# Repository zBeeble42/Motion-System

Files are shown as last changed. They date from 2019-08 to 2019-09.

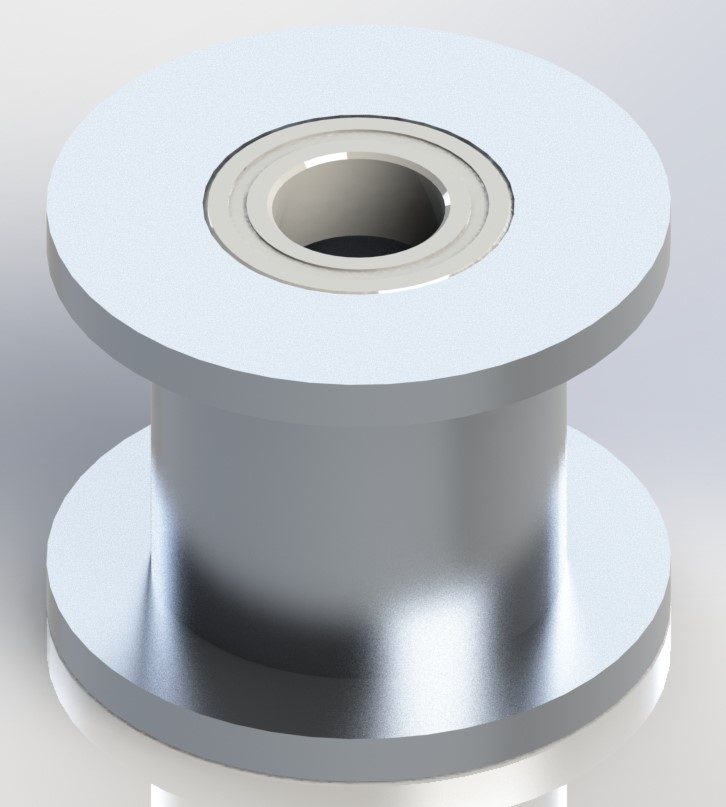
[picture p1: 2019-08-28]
Solidworks/1037396.JPG

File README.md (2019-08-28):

# Motion System
STPs / STLs / DXFs / PDFs

E3D-Online Ltd: Copyright (C) E3D-Online Ltd (e3d-online.com) These files are free hardware you can redistribute it and / or modify it under the terms of the General Public License as published by the Free Software Foundation, either version 3 of the License, or (at your option) any later version.
McMaster Carr: Copyright (C) McMaster Carr (mcmastercarr.com) The CAD models are being made available to help you decide whether to purchase products from us.  No other use is authorized or granted.
  
---------------------------------------------------------------------------------------------------------------------------------------
TODO:
 - Add in the purchasable hardware.
 - Modify the toolhead printed boden tube\wire harness mount to be one printed item and strain relief the boden tube and wire harness better.
 - Finish the Bondtech BMG-M toolhead assembly.
 - Create 
---------------------------------------------------------------------------------------------------------------------------------------
TIMELINE:
 08/28/19 - (Me) Added progress to the motion system assembly, and updadted the BOM with purchasable items (some to replace machineable parts from the E3d Github master repo).  I also added an "attempt" to create a tool head for the Bondtech BMG-M direct drive extruder. 

 08/15/19 - (Me) Added BOM

 08/13/19 - (Me) Forked from E3D Online, and started adding Solidworks 2017 files

 05/08/19 - (E3D) Added README.md to the STLs folder  

 02/08/19 - (E3D) Added assembly drawings

 31/07/19 - (E3D) Added step files of printed parts

 30/07/19 - (E3D) Initial Upload

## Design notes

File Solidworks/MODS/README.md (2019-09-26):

This modified version of E3D's toolchanger uses a more commonly found 24BYJ48 micro stepper motor with the two "ears".

The machined aluminium 'TC-BACK_1_1.sldprt' -> 'TC_BACK_1_2.sldprt' and 
the 3D printed 'Tool-Changer Cover Body.sldprt' -> 'Tool-Changer Cover Body_1.1.sldprt' 
parts have been modified to fit these motors.

I have not tested any motors with this new design, so use this at your own risk.

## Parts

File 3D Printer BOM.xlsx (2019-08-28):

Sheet: Hardware
Item # | Description | Supplier | Part Number | Qty | Units | Cost/Pc | Pur Cost | Order Qty | CAD?
1 | Knife |  |  | 1 | ea
2 | 5mm Allen Key |  |  | 1 | ea
3 | 4mm Allen Key |  |  | 1 | ea
4 | 2.5mm Allen Key |  |  | 1 | ea
5 | 2mm Allen Key |  |  | 1 | ea
6 | Bubble Level |  |  | 1 | ea
7 | Machinist Square |  |  | 1 | ea
8 | Gel Thread Lock (Blue) | McM | 1810A3 | 1.69 | floz |  | $28.93 | 1.69
9 | Isocyanate Glue |  |  | 1 | floz
10 | Small Side Cutters |  |  | 1 | ea
47 | Thickened PTFE Grease |  |  | 0.75 | floz
11 | M3 Thread Tap | McM | 2541A31 | 1 | ea |  | $15.80 | 1
12 | M8 Thread Tap | McM | 2541A35 | 1 | ea |  | $19.20 | 1
13 | 25-2560 x 500mm Al Extrusion |  |  | 4 | ea
 | M2 x 6mm SHCS
14 | M2 Washers | McM | 93475A195 | 8 | ea |  | $1.06 | 100 | Yes
15 | M2.5 x 5mm SHCS | McM | 91292A009 | 1 | ea |  | $4.97 | 100 | Yes
16 | M3 x 3mm FHCS |  |  | 4 | ea
17 | M3 x 5mm BHCS | McM | 92095A177 | 7 | ea |  | $6.12 | 100 | Yes
18 | M3 x 8mm SHCS | McM | 91292A112 | 4 | ea |  | $4.52 | 100 | Yes
19 | M3 x 8mm FHCS | McM | 92125A128 | 4 | ea |  | $3.54 | 100 | Yes
20 | M3 x 10mm SHCS | McM | 91292A113 | 1 | ea |  | $4.97 | 100 | Yes
21 | M3 x 10mm BHCS | McM
22 | M3 x 12mm FHCS | McM | 92125A132 | 24 | ea |  | $4.97 | 100 | Yes
23 | M3 x 12mm BHCS
24 | M3 x 16mm FHCS | McM | 92125A134 | 8 | ea |  | $8.28 | 100 | Yes
25 | M3 x 30mm BHCS
26 | M3 x 45mm BHCS
27 | M3 x 50mm FHCS | McM | 92125A151 | 2 | ea |  | $6.70 | 50 | Yes
28 | M3 x 10mm Low Profile Sholder Screw | McM | 90323A215 | 10 | ea |  | $2.75 | ea >5
31 | M3 x 3mm Grub Screw |  |  | 1 | ea
32 | M3 x 12mm PEEK Standoffs |  |  | 4 | ea
33 | M3 Standoffs | McM | 93655A419 | 10 | ea |  | $3.20 | ea >10 | Yes
 | M3 x 4mm unthreaded standoff (replaces MS-XY-STOP) | McM | 92871A173 | 4 | ea
34 | M3 x 24mm (6mm hex) (Replaces MS-SOFF-M3-FF-24L) | McM | 94868A743 | 2 | ea |  | $6.61 | ea | Yes
29 | M3 Washers | McM | 93475A210 | 62 | ea |  | $1.62 | 100 | Yes
30 | M3 Hex Half Nuts |  |  | 4 | ea
35 | M4 x 3mm Grub Screw |  |  | 1 | ea
36 | M4 x 8mm BHCS |  |  | 16 | ea
37 | M4 x 6mm BHCS |  |  | 17 | ea
38 | M4 x 12mm BHCS |  |  | 4 | ea
39 | M4 x 16mm BHCS |  |  | 2 | ea
40 | M4 x 10mm BHCS |  | 92095A190 | 4 | ea |  | $9.05 | 100 | Yes
41 | M4 x 10mm Low Profile Sholder Screw (Replaces MS-SHAFT-BOLT) | McM | 90318A810 | 10 | ea |  | $3.13 | ea >5 | Yes
 | M4 x 4mm - 6mm OD Standoffs (Replaces MS-Z-STOP) |  | 92871A006 | 2 | ea |  | $1.89 | ea | Yes
42 | M4 x 12mm Standoffs |  |  | 8 | ea
43 | M4 Washers |  | 93475A230 | 15 | ea |  | $1.86 | 100 | Yes
44 | M4 Nylon Washers |  |  | 8 | ea
45 | M4 Hex Half Nuts |  |  | 2 | ea
46 | M6 T-Nuts |  | 5537T527 | 28 | ea |  | $5.08 | 4
47 | M6 x 10mm BHCS |  |  | 25 | ea
48 | M6 Washers |  |  | 24 | ea
49 | M6 Grub Screw |  |  | 4 | ea
50 | M8 Feet | McM | 6301K79 | 5 | ea |  | $6.20 | 1
51 | M8 x 20mm BHCS |  | 92095A284 | 15 | ea |  | $13.64 | 25
52 | E-Clip |  | 98317A214 | 1 | ea |  | $9.86 | 50
53 | 3mm x 12mm Dowel |  | 91595A112 | 1 | ea |  | $8.62 | 50
54 | 1mm x 4mm Dowel |  | 91585A034 | 6 | ea |  | $8.63 | 100
55 | Thickened PTFE Grease |  |  | 0.75 | floz
56 | MR1052ZZ bearing |  | 7804K106 | 1 | ea |  | $7.60 | 1
57 | SF695ZZ Bearing (695-2Z) |  | 7804K138 | 1 | ea |  | $9.20 | 1
58 | F5-12M bearing |  | 7806K57 | 1 | ea |  | $8.66 | 1
59 | Spring |  |  | 1 | ea
60 | Zip Ties
61 | Fray-Resistant Expandable Sleeving, Fray-Resistant, 1/8" ID |  |  | 10 | ft
62 | Braided Sleeve
63 | Metal Strips |  |  | 5 | ea
64 | 2.54mm Crimp Terminal (22-28 Gauge) |  |  | 100 | pcs
65 | 790mm lengths of PTFE tubing |  |  | 4 | ea
66 | 850mm lengths of PTFE tubing |  |  | 4 | ea
67 | Lay-in Snap-Together Open Cable/Hose Carrier for 0.5" Maximum Cable OD/0.5" Total Cable Width, 0.9" High |  |  | 1 | ft
68 | 6.25mm x 7.0mm Neodymium Magnet |  |  | 4 | ea

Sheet: Electrical
Item # | Description | Part Number | Qty | Units
 | Duet2 WiFi/ Ethernet |  | 1 | ea
 | DueX5 |  | 1 | ea
 | Power Supply - S-400-24 |  | 1 | ea
 | SSR G3NA-210B-UTU |  | 1 | ea
 | 300mm x 200mm Heated Bed 24VDC |  | 1 | ea
 | Duet Wiring Kit |  | 1 | ea
 | Panel Mount RJ45 Connector |  | 1 | ea
 | Axis Motors (1.8deg @ 2A) | Moons MS17HD2P4200 | 2
 | Extruder motors | MOTECH MT-1703HSM1168RE .9 deg/step | 4
 | X-Axis Hiwin Rail | MGNR9H 180dq 10200 | 1
 | Y-Axis Hiwin Rail | MGNR12H 180DQ 5000 | 2
 | Z-Axis Hiwin Rail | MGWR12H 180DQ0 40100 | 1

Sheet: 3D Printed Parts
Item # | Description | Qty | Units
 | Printed V6 Dock Cables | 2
 | Printed V6 Dock Cables (Mirror) | 2
 | Printed Spool Carrier | 4
 | Printed Filament Pick-Up | 4
 | Printed PSU Duct | 1
 | Printed Cable Blank | 1
 | Printed RJ45 Cable Blank (Optional) | 1
 | Printed Wiper Brush Holder | 1
 | Printed IEC Socket | 1
 | Printed IEC Bracket | 1
 | Printed X-Carriage Cable Bracket | 2
 | Printed Tool-Changer Cover | 1
 | Printed Motor Cable Cover | 1
 | Printed Z-Axis Motor Cable Cover | 1
 | Printed MS-BELT-CLAMP | 4

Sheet: Machined Parts
Item # | Description | Qty | Units
1 | 8mm x 90mm Metal Bar (Spool Bar) | 4
5 | MS-LONG-PULLEY-STANDOFF | 4
6 | MS-MOTOR-SPACE-SHORT | 4
7 | MS-SOFF-M3-FF-24L_1 | 2
8 | MS-SHAFT-BOLT | 10
9 | MS-SHORT-PULLEY-STANDOFF | 10
10 | MS-TOP-PLATE | 1
11 | MS-BASE-PLATE | 1
12 | MS-SIDE-PANEL | 2
13 | MS-ELEC-PANEL | 1
14 | MS-REAR-PANEL | 1
15 | MS-BED-BRACKET | 1
16 | MS-TENSION-BLOCK | 2
17 | MS-TENSION-ARM | 2
18 | MS-Z-STOP | 2
19 | MS-XY-STOP | 4
20 | Z-Axis Bed Bearing Bracket | 1
21 | Z-Axis Angle Motor Bracket | 1
22 | X-Plate | 1
23 | Z-AXIS BED PLATE | 1
24 | MS-X-BELT-PLATE | 1
25 | MS-X-BLOCK | 1
26 | MS-X-SPACER | 2
27 | MS-BED-BRACKET | 1
28 | TC-MOD 0.5-20T-SERVO-GEAR | 1
29 | TC-MOTOR-BRACKET | 1
30 | TC-FACE | 1
31 | TC-HE-V6 | 1
32 | TC-V6-DOCK | 4
33 | TC-DOCK-V6 | 1
34 | TC-PLATE | 1
35 | TC-RAMP-6MM | 1
36 | TC-BACK | 1
37 | TC-DOCK-PIN-V6 | 8
38 | TC-SHAFT | 1

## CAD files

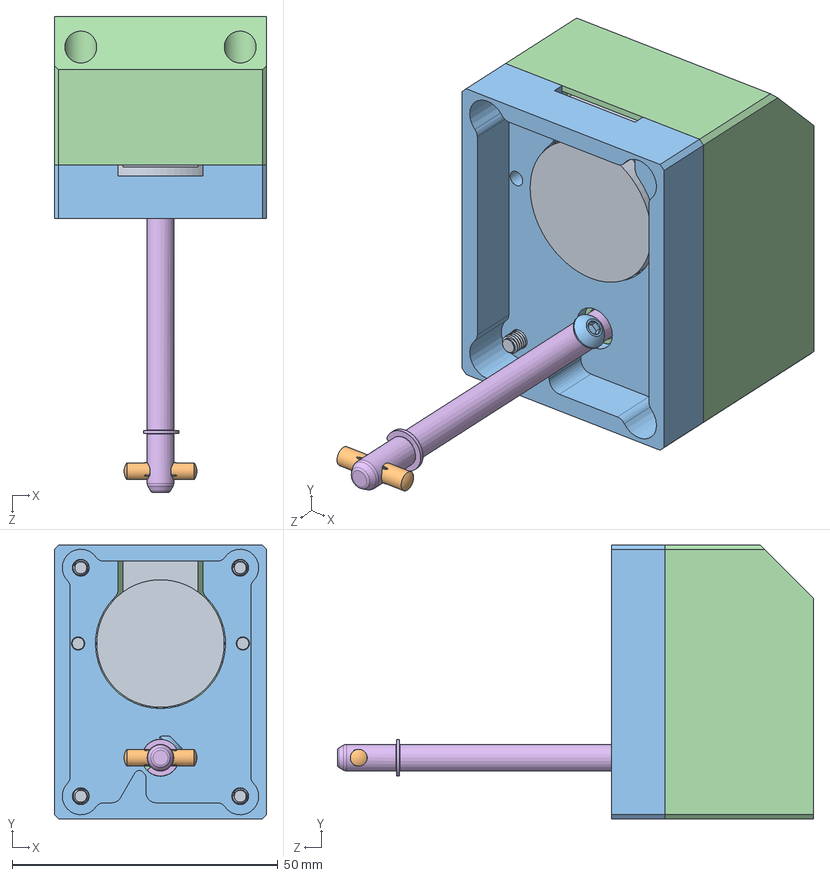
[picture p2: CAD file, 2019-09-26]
Solidworks/MODS/Tool Changer Front v2.sldasm
40.0 x 51.5 x 89.6 mm
93655A419_MALE-FEMALE THREADED HEX STANDOFF x 6
91292A110_TYPE 18-8 SS SOCKET HEAD CAP SCREW x 4
92095A471_18-8 SS BUTTON-HEAD SOCKET CAP SCREW x 4
7804K106_STAINLESS STEEL BALL BEARING MR105RS
7806K570_F5-12 Thrust bearing
98543A103_SIDE-MOUNT EXTERNAL RETAINING RING E-STYLE
94125K671_COMPRESSION SPRINGS
98269A420_BLACK-OXIDE 18-8 STAINLESS STEEL FLAT WASHER
91390A097_ALLOY STEEL CUP POINT SET SCREW
98400A237_GROOVED DOWEL PIN
TC-BACK_1_2
Tool-Changer Cover Body_1.1
Caution Label^Tool-Changer Cover Body Asm_1.0
TC-SHAFT 1.5
Spur Gear (20 teeth)
Spur Gear (40 teeth)
24BYJ-48 Stepper Motor

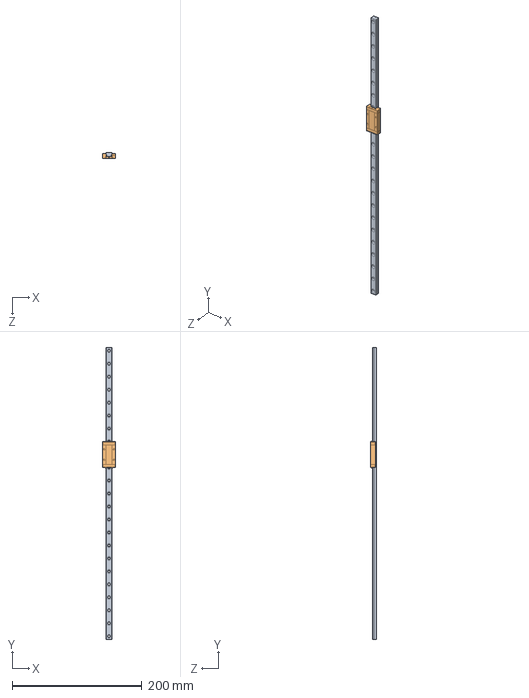
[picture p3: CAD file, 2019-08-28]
Solidworks/X-Axis_Hiwin Rail MGN09H1R450Z0HM.SLDASM
20.0 x 450.0 x 10.0 mm
MGN09H1R450Z0HM_FILE(2)
MGN09H1R450Z0HM_FILE

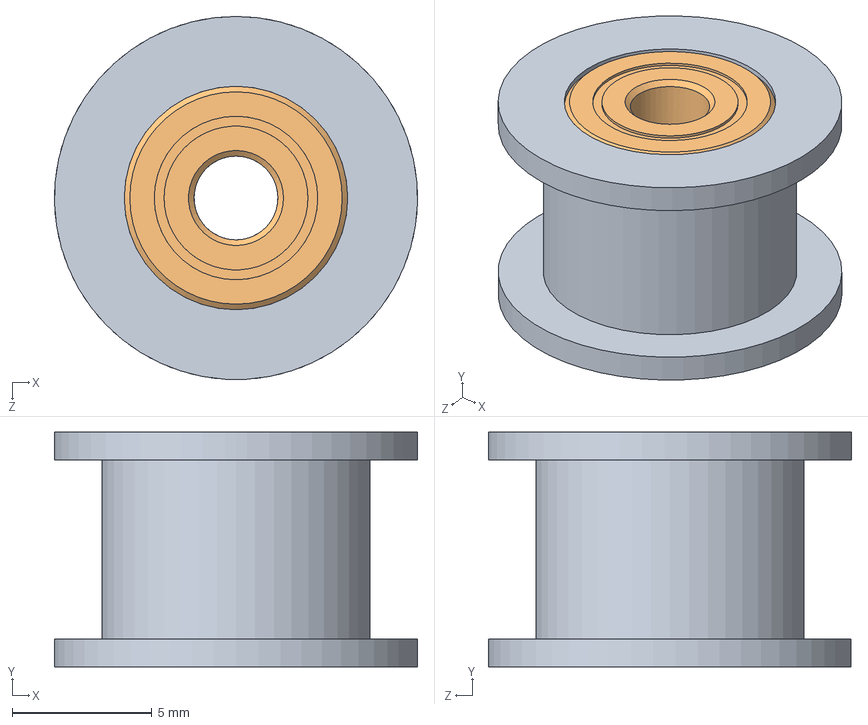
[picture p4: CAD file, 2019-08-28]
Solidworks/16T W6 B3 Without T.SLDASM
13.0 x 8.40 x 13.0 mm
16T W6 B3 Without T, Idler Pulley
16T W6 B3 Without T, 693-2Z BEARING, 8 mm OD, 3 mm ID, 4 mm WIDTH x 2

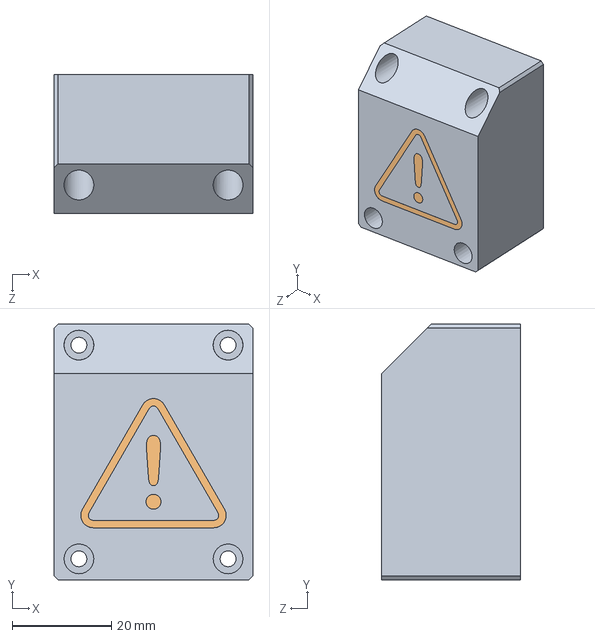
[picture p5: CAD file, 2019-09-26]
Solidworks/MODS/Tool-Changer Cover Body Asm_1.0.SLDASM
40.0 x 51.5 x 28.0 mm
Tool-Changer Cover Body_1.1
Caution Label^Tool-Changer Cover Body Asm_1.0

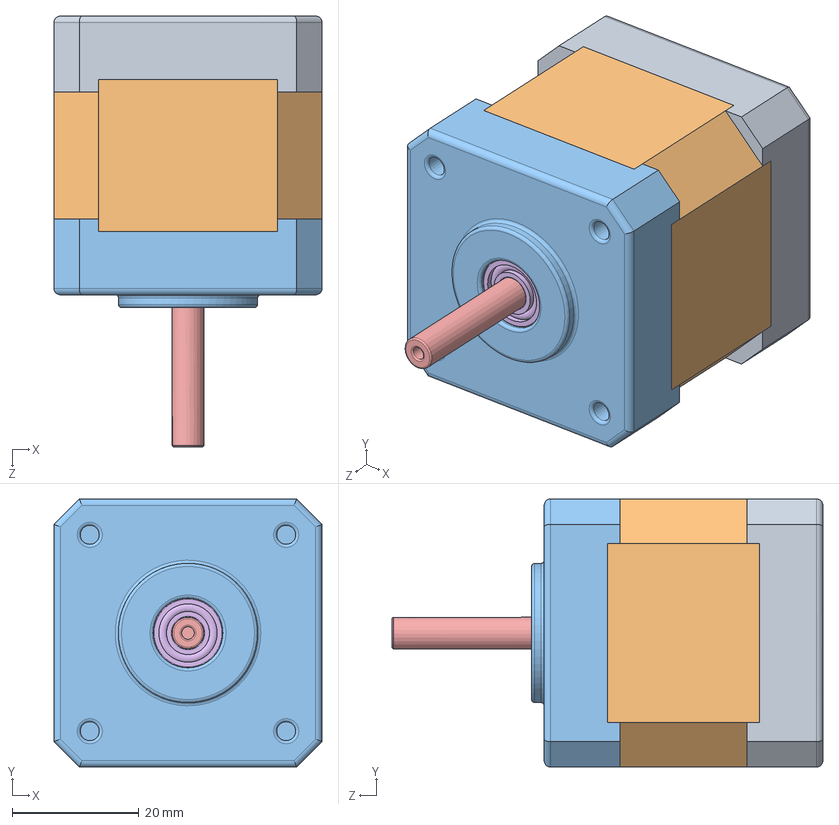
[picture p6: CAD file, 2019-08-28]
Solidworks/NEMA 17.SLDASM
42.3 x 42.3 x 68.0 mm
Base
Cuerpo
Tapa
pan cross head_am x 4
Eje
instrument ball bearing_68_am x 2

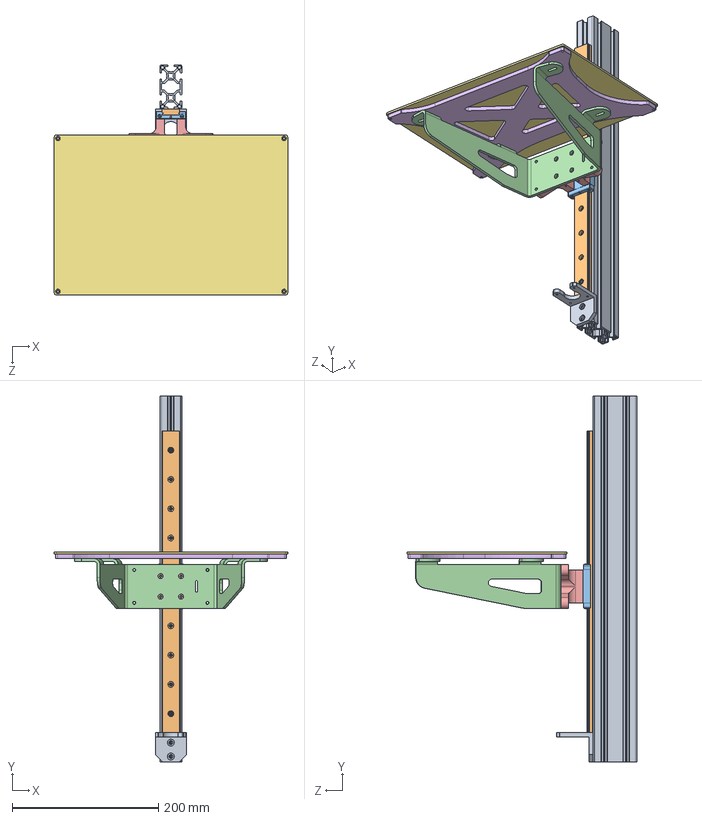
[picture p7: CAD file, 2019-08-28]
Solidworks/Z-Axis Asm.SLDASM
319.0 x 500.0 x 314.5 mm
8020-30-3060 X 4000
MGW12H1R412Z0HM_FILE(2)
MGW12H1R412Z0HM_FILE
MS-BED-BRACKET 1.4
Z-Axis Bed Bearing Bracket
Z-Axis Bed Plate
300X200MM XL ALUMINUM BUILD PLATE
MS-Z-STOP 1.0 x 2
Z-Axis Angle Motor Bracket

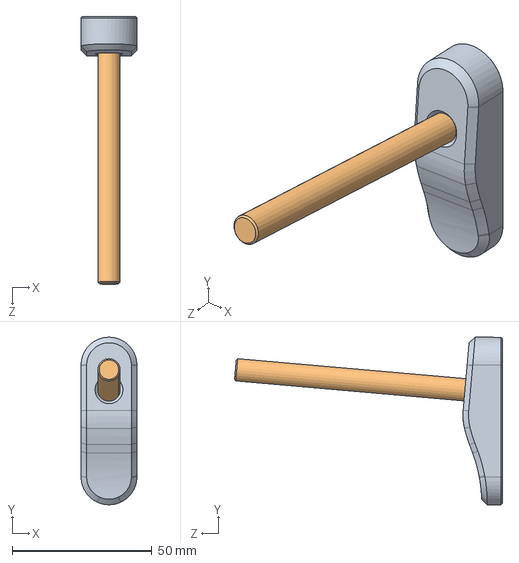
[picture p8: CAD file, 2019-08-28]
Solidworks/Spool Carrier ASM.SLDASM
20.0 x 60.0 x 95.9 mm
Spool Carrier
Spool Bar

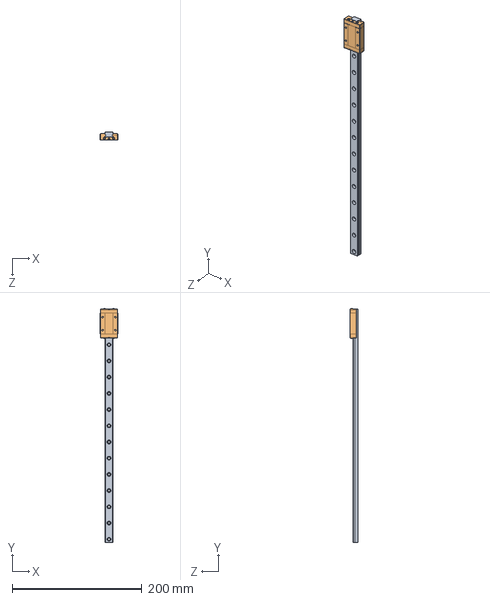
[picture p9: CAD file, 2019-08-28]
Solidworks/Y Axis_Hiwin Rail MGNR12R-360-H-M-E5.SLDASM
27.0 x 360.9 x 13.0 mm
Y-Rail
Y-Slide

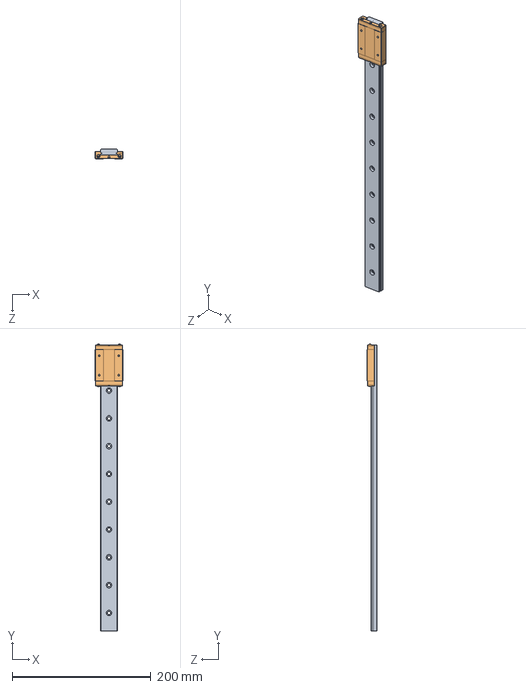
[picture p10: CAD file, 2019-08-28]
Solidworks/Z-Axis_Hiwin Rail MGW12H1R412Z0HM.SLDASM
40.0 x 413.1 x 14.0 mm
MGW12H1R412Z0HM_FILE(2)
MGW12H1R412Z0HM_FILE

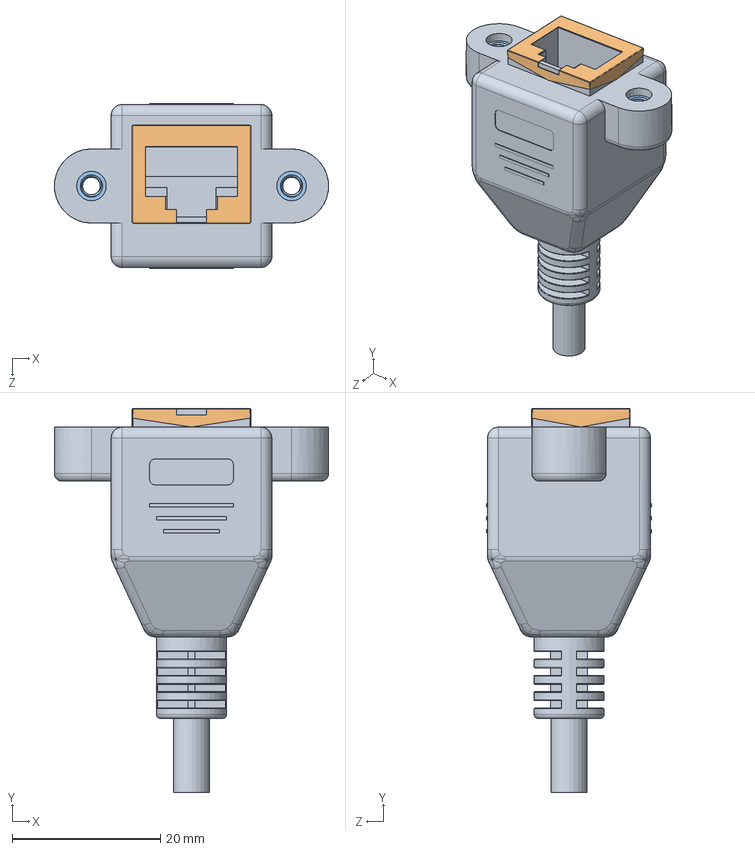
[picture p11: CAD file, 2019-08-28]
Solidworks/RJ45 PanelMount.SLDASM
37.0 x 51.8 x 22.2 mm
RJ45
MetalSheet
M3 - nut 92497A200 v1 x 2

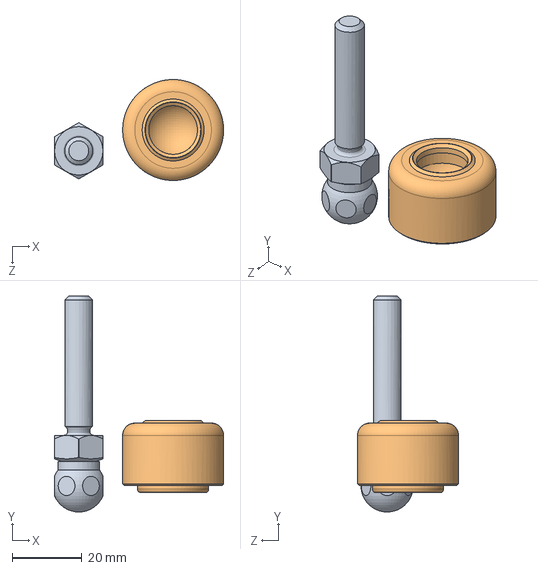
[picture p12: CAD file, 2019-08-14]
Solidworks/Frame Foot.SLDASM
48.6 x 62.0 x 29.0 mm
8020-12195-$PARTNUMBER
8020-DEFAULT

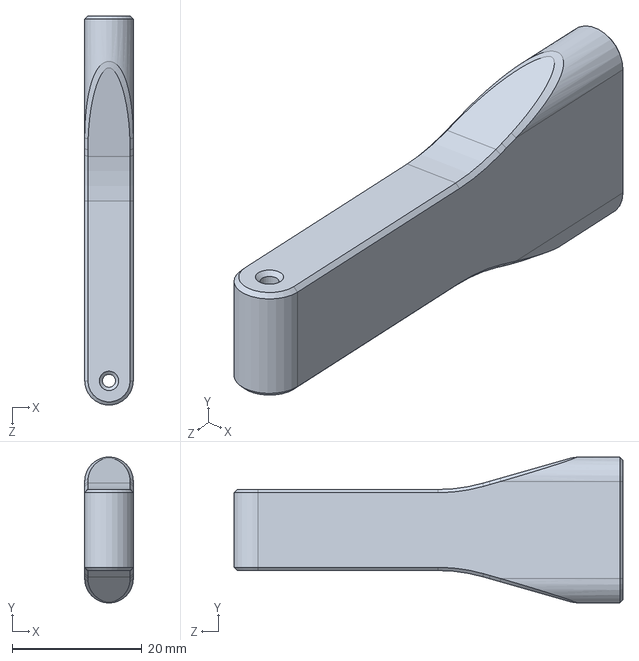
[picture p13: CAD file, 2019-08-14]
Solidworks/Filament Pick-Up.SLDASM
7.50 x 22.5 x 60.0 mm

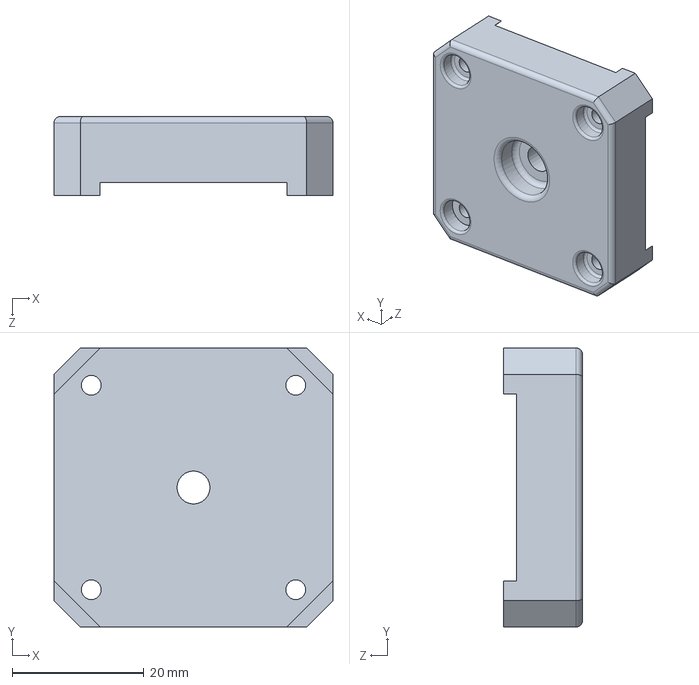
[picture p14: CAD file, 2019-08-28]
Solidworks/Base.SLDPRT
42.3 x 42.3 x 12.0 mm

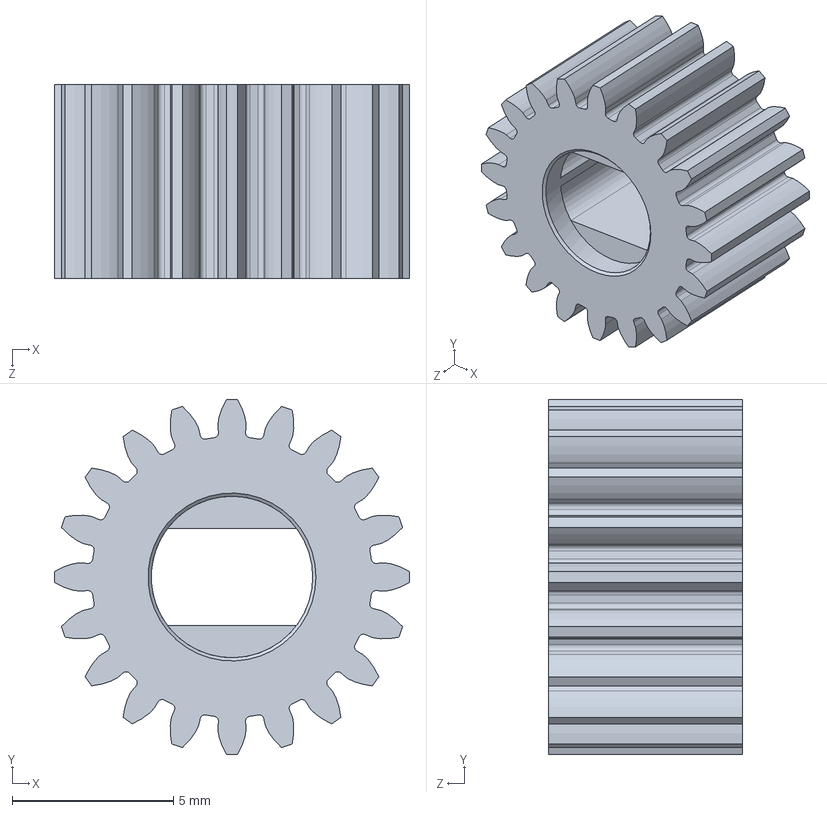
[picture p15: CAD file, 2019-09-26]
Solidworks/MODS/Spur Gear (20 teeth).sldprt
11.0 x 11.0 x 6.00 mm

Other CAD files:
Solidworks/AFDF9_20.sldasm
Solidworks/GPA20MR2060_A_H5.sldasm
Solidworks/Wiper.sldprt
Solidworks/MS-BED-BRACKET 1.4.SLDPRT
Solidworks/1037396-95-2Z BEARING, 9 mm OD, 5 mm ID, 3 mm WIDTH.SLDPRT
Solidworks/1037396-IDLER PULLEY.SLDPRT
Solidworks/1037396.SLDASM
Solidworks/1037396.STEP
Solidworks/1037396.x_b
Solidworks/16T W6 B3 Without T, 693-2Z BEARING, 8 mm OD, 3 mm ID, 4 mm WIDTH.SLDPRT
Solidworks/16T W6 B3 Without T, Idler Pulley.SLDPRT
Solidworks/21.5mm Spacer.sldprt
Solidworks/25-2550.SLDPRT
Solidworks/300X200MM XL ALUMINUM BUILD PLATE.SLDPRT
Solidworks/4409T225_SNAP-TOGETHER CABLE AND HOSE CARRIER.SLDPRT
Solidworks/55835K121_SNAP-TOGETHER CABLE AND HOSE CARRIER.SLDPRT
Solidworks/8020-12195-$PARTNUMBER.SLDPRT
Solidworks/8020-30-3060 X 4000.SLDPRT
Solidworks/8020-DEFAULT.SLDPRT
Solidworks/Cable Blank RJ45_1.sldprt
Solidworks/Cable Blank_1.sldprt
Solidworks/Cuerpo.SLDPRT
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

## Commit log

2019-08-14 Initial Fieles
    [21.5mm Spacer.sldprt, 25-2550.SLDPRT, 4409T225_SNAP-TOGETHER CABLE AND HOSE CARRIER.SLDPRT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]
2019-08-15 Initial Upload
    Bill of materials for the E3D Motion Platform and Tool Changer
    [3D Printer BOM.xlsx]
2019-08-28 Completed the main assembly
    Completed the main assembly
    Added purchasable components to replace machined versions. Refer to the BOM for details.
    [1037396-95-2Z BEARING, 9 mm OD, 5 mm ID, 3 mm WIDTH.SLDPRT, 1037396-IDLER PULLEY.SLDPRT, 1037396.SLDASM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]
2019-08-28 Updated BOM
    Added more purchasable parts.
    [3D Printer BOM.xlsx]
2019-09-26 Initial Upload
    [TC-BACK_1_2.sldprt, Tool-Changer Cover Body_1.1.sldprt]
